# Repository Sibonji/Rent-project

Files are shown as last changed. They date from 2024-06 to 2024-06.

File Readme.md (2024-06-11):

# Проект: Вендинговый шкаф для аренды приборов (Phystech Rent)

## Команда:
Мухина Анфиса Дмитриевна: Дизайн модели большого шкафа; Создание 3д модели прототипа шкафа; Сборка прототипа; Построение схемы и тестирование замка
Сигбатулин Булат: Разработка веб интерфейса; Создание 3д модели прототипа шкафа; Сборка прототипа; Настройка взаимодействия сервера с NSP32.
Мотриченко Арсений: Создание 3д модели прототипа шкафа; Сборка прототипа; Дизайн веб интерфейса; Закупка комплектующих
Нвер Авагимян: Создание 3д модели прототипа шкафа; Сборка прототипа; Закупка комплектующих

## Описание продукта:
Необходимые предметы для быта занимают слишком много места, невзвешенные покупки, которые пылятся на полках, вещи, которые стоят стоят слишком дорого. Все эти проблемы может решить наш проект — вендинговый шкаф с почасовой арендой необходимой техники от пылесоса до плей стейшн.

Наш проект состоит из: шкафа, в котором будут храниться вещи для аренды, и сайта, через который можно бронировать определённый слот и завершать бронь, после использования.

## Цель работы
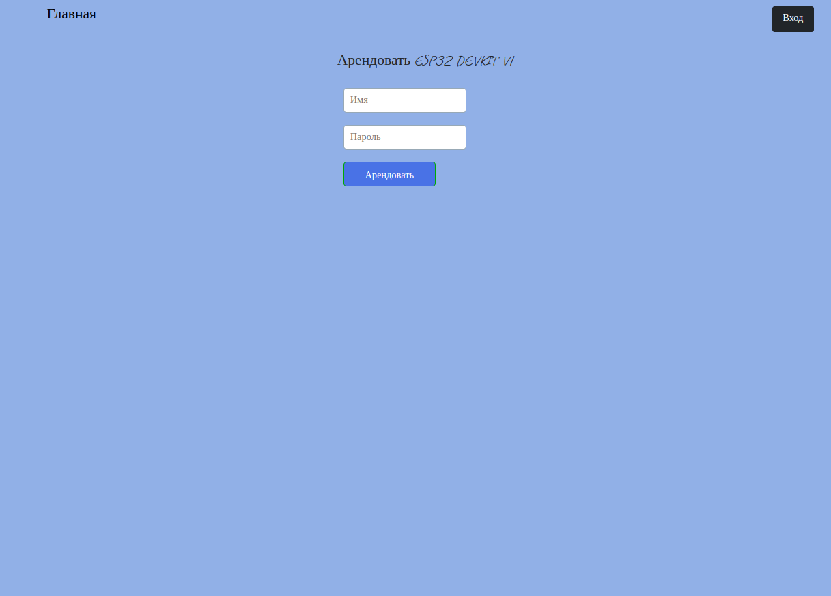
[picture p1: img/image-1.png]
Разработать прототип устройства и сервиса для удобной аренды различных вещей: бытовой техники, электронных комплектующих, инструментов и т.д. При некоммерческом использовании данное устройство может облегчить заимствование различных электронных устройств в Радиотехнической комнате (находится в 1 общежитии), Физтех Фабрике и на других площадках МФТИ. С помощью него можно будет избавиться от прослойки в виде ответственного за выдачу человека, иметь возможность "арендовать" (бесплатно) нужную вещь в любой время, а ответственному - просто и быстро отслеживать кто и когда взял в использование определенный предмет.

## Задачи

В ходе работы нужно будет решить несколько основных задач:
 - Посмотреть на существующие решения, и определить размеры и используемые материалы и комплектующие для нашего прототипа
 - Смоделировать прототип в специализированной программе (SolidWorks)
 - Собрать прототип
 - Релизовать программную модель прототипа
 - Релизовать сервис, через который будет осуществляться "аренда" в прототипе

## Анализ существующих аналогов

### Tulu

Это зарубежная компания, её нет на Российском рынке.

О постмате. В основном корпус выполнен из дерева, но имеются железные вставки. Такой выбор материала обеспечивает красивый вид, однако фанера, является более крепким материалом. Двери выполнены из стекла, это не самый надёжный вариант, но зато клиент может чётко видеть вещи, доступные к аренде, и их состояние. Замок на постматах Tulu не оснащён толкателем, он помогает клиенту понять, какой именно отсек активировался и облегчает открытие дверей, если в них нет ручек, но у шкафов Tulu дверцы прозрачные и в них добавлены ручки, что решает проблему.

Больгим приемуществом является доступность предметов для аренды, клиент не должен ждать достаку, и может сразу забрать продукт. В приложении есть временная гибкость, для вещей предусмотрена почасовая оплата. В отзывах люди жалуются на плохую работу приложения, например, польщователь переустанавливал его 3 раза прежде чем приложение заработало. Так же клиенты отмечают трудности с завершением аренды: приложение зависает и не даёт завершить аренду, в то время как деньги за арендованную вещь продолжают начисляться. Помимо всего прочего пользователи отмечают плохую работу поддержки, которая долго отвечает на сообщения, из-за этого у людей не получается вовремя решить проблему и они теряют деньги и время. 

### Арентер

Корпус постмата выполнен из железа, что даёт повышенную устойчивость к огню и воде. Часть дверей выполнены из стекла, часть полностью из железа не позволяя клиентам видеть, что находится внутри. На дверцах отсутствуют ручки, однако в ячейках стоят удобные замки с толкателем, что позволяет удобно открывать и закрывать дверь.

Арентер, как сервис по аренде, давно существует на Российском рынке, но аренду в формате постмата они ввели меньше месяца назад. По большей части эта компания ориентируется на то, что клиент сначала заказывает товар со склада, ждёт доставку и уже потом забирает предмет, это уменьшает доступность, поскольку клиент получает товар не сразу. Однако их приложение и предметы для аренды можно рассмотреть. У данного сервиса сложности с автоматизацией: непонятные цены, пользователи отмечают, что информация о ценах в приложении отличается от реальной, нет точной информации о том, что доступно в аренду, а что нет, любые вопросы уточняются через оператора, который зачастую отсутствует. 

### Наш вариант

Исследовав аналоги, мы поняли, что большое внимание стоит уделить приложению для аренды, нужно сделать его максимально прозрачным и минимизировать проблемы, о которых говорилось в отзывах у других компаний. Также мы решили реализовывать приложение в виде веб-интерфейса, так как это минимизирует проблемы, которые могут возникать из-за плохой поддержки приложения на разных устройствах. Рассмотрев различные реализации дверей постматов мы выбрали вариант со стеклом, это повышает заинтересованность пользователей и показывает, что вещи, хранящиеся в шкафу в надлежащем качестве. Возможно это не самый надёжный вариант, но в общежитии, где планируется применять наш шкаф, много камер, что повышает безопасность. Для уверенности можно привести в пример работу сервиса Self, который продаёт еду. Их товар лежит на полках, никак не закрытый, безопасность гарантируют качественные камеры, установленные на полках с товаром. Каркас нашего прототипа было решено сделать из фанеры, это надёжный и доступный материал. Для наилучшего скрепления составных частей шкафа мы сделали шиповое соединение у деталей. Двери мы решили делать без ручек в рамках экономии, удобное открытие гарантирует замок, который толкает дверь, чтобы она открылась широко. В качестве примера, на который мы впоследующем будем опираться, был нарисован примерный дизайн готового устройства:

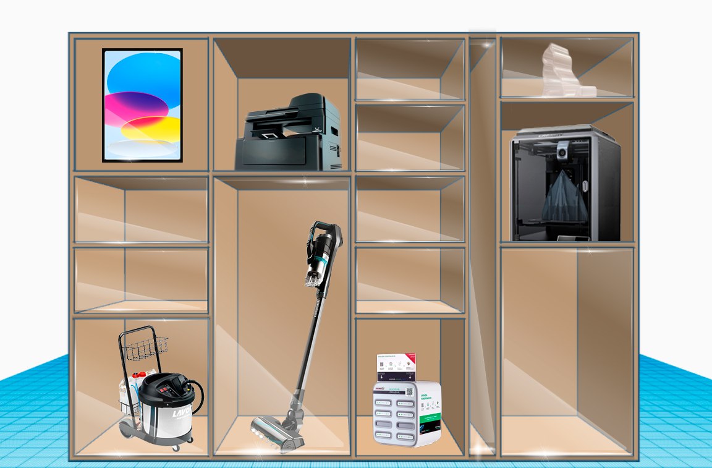
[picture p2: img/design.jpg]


## Ход работы

### Разработка корпуса

Модель разрабатывалась в приложении SolidWorks, в виде отдельных деталей, которые потом были объединены в виде сборки в том же приложении (детали и готовую сборку можно найти в папке box). Так как корпус будет вырезан из дерева было решено использовать для этого фрезерный станок, но перед этим, чтобы не тратить много дерева при неудаче, вырезать мини-модель с помощью лазерной резки:

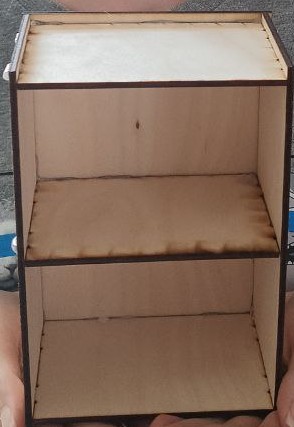
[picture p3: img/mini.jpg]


После того, как мы убедились что все корректно собралось на фрезерном станке, из фанеры толщиной 12мм, был вырезан корпус протипа:

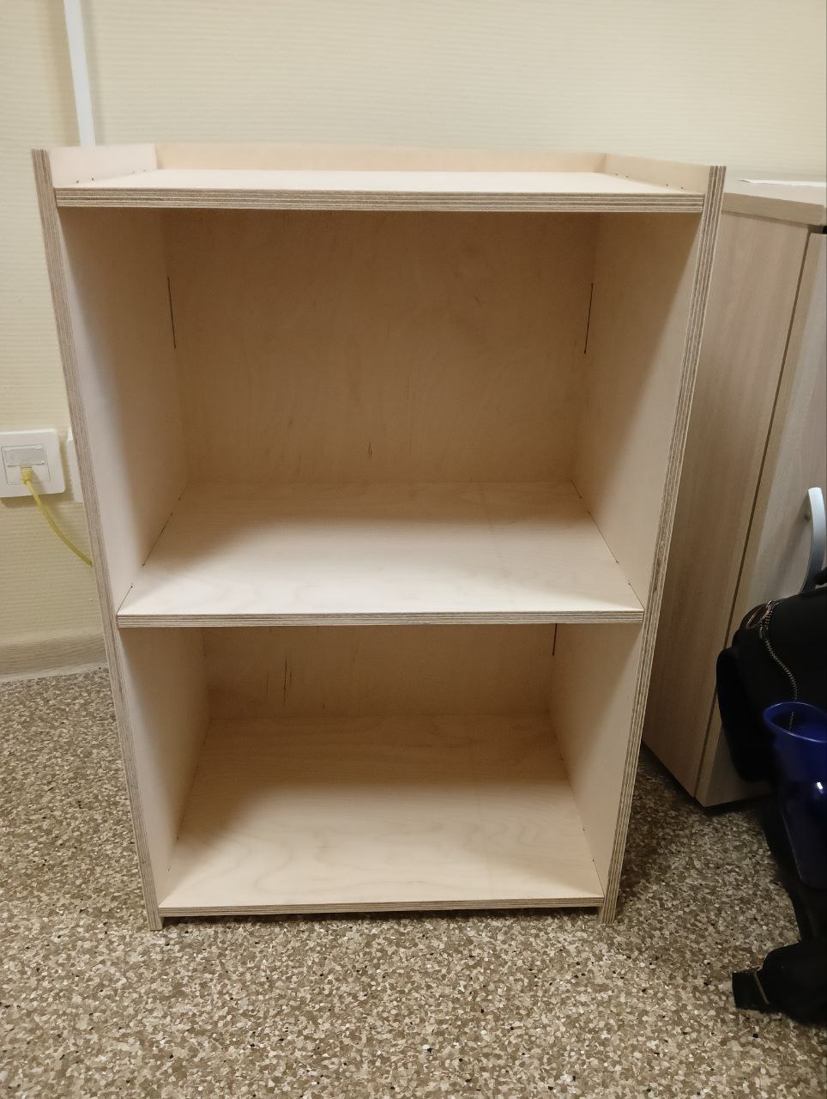
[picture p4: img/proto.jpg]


В завершении к корпусу были прикручены петли с стеклянными дверьми и электронные замки.

### Разработка электрической схемы

Теперь требуется определить электронную составляющую прототипа. Этим стали:

 - ESP32 - микроконтроллер, принимающий сигналы от веб сервера и управляющий замками.
 - XG07E Electronic Miniature Plastic Titanium Lock - замок используемый для открывания двери, с рабочим напряжением на входе.
 - Транзисторы TIP122 и резисторы на 1КОм для проектирования надежной электрической схемы открывания замка.

На картинке снизу представлена схема устройства, в качестве изображения замка используется схема элемента "логическое и":

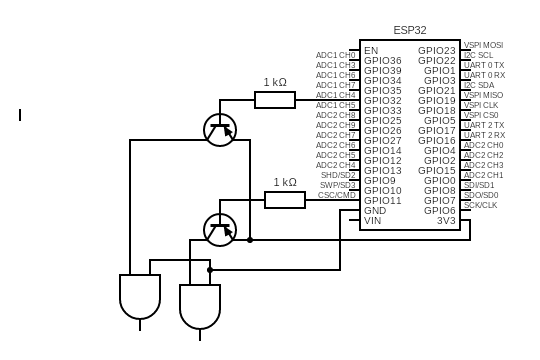
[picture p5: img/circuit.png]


Питание ESP32 в прототипе реализуется при помощи подключенного к порту micro-usb портативного зарядного устройства.

### Разработка сервера (веб-интерфейса) и клиента (код ESP32)

Сайт работает на основе библиотеки Flask (Python) с использованием баз данных под управлением MySQL. Данные хранятся в двух базах данных:
 - БД с пользователями (db/postamates.db)
 - БД с постаматами (user.db)

БД с пользователями хранит в себе одну таблицу - с информацией о пользователях:
 - Имя
 - Хэш пароля
 - Номер телефона

БД с постаматами хранит в себе 2 таблицы, таблицу с информацией о постаматах:
 - Id постамата
 - Ip адрес постамата (ESP32)
 - Расположение постамата

И таблицу с информацией о ячейках в каждом постамате:
 - Id постамата
 - Id ячейки (привязана к пину GPIO на ESP32, через который ячейка открывается)
 - Статус ячейки (есть ли там что-то или нет)
 - Id пользователя, который в последний раз оттуда что-то брал
 - Дата и время, когда оттуда что-то брали в последний раз
 - Информация о предмете, который там лежит

Код ESP32, хоть и называется клиентом, в свою очередь также является небольшим веб-сервером. Он представляет собой набор ссылок строящихся по шаблону - <esp_ip_addr>/<GPIO_PIN>/on. Здесь:
 - esp_ip_addr это ip адресс присваеваемый ESP
 - GPIO_PIN - номер пина GPIO, который управляет открытием и закрытием определенной ячейки.

При бронировании и возвращении предмета в ячейку, сайт (сервер) обращается по соответствующей ссылке ESP32 (клиента), а тот в свою очередь считывает это обращение и открывает ячейку. Открытие ячейки занимает определенное время из-за электрических характеристик замка. При входном напряжении 3 Вольта замку требуется чуть меньше 1 секунды на открытие, так как напряжение с выхода ESP32 подается сразу на два замка, это время было увеличено до 1,5 секунд, чтобы обеспечить стабильную работу устройства. Для бронирования необходимо перейти на сайт, выбрать постамат в нужной локации и устройство, которое вы хотите взять:

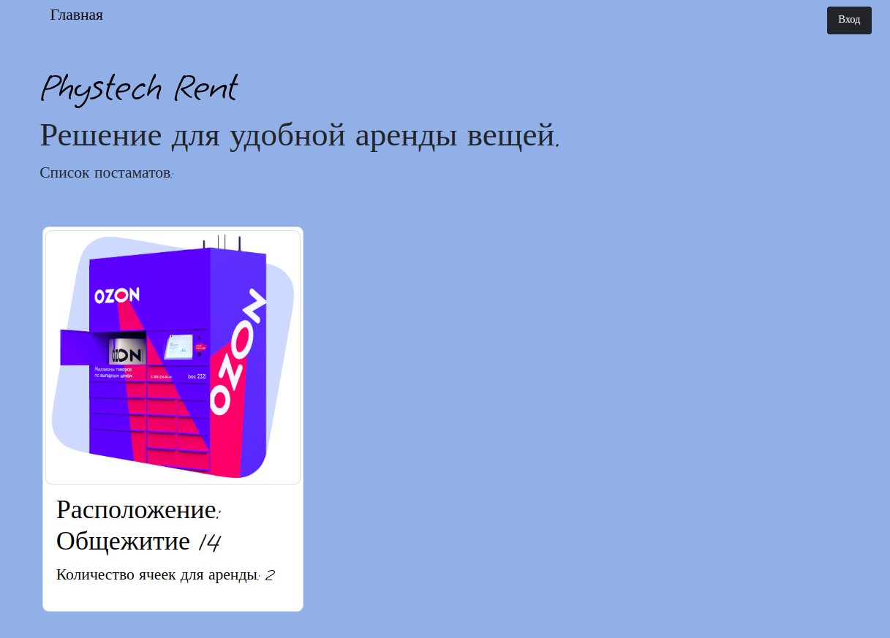
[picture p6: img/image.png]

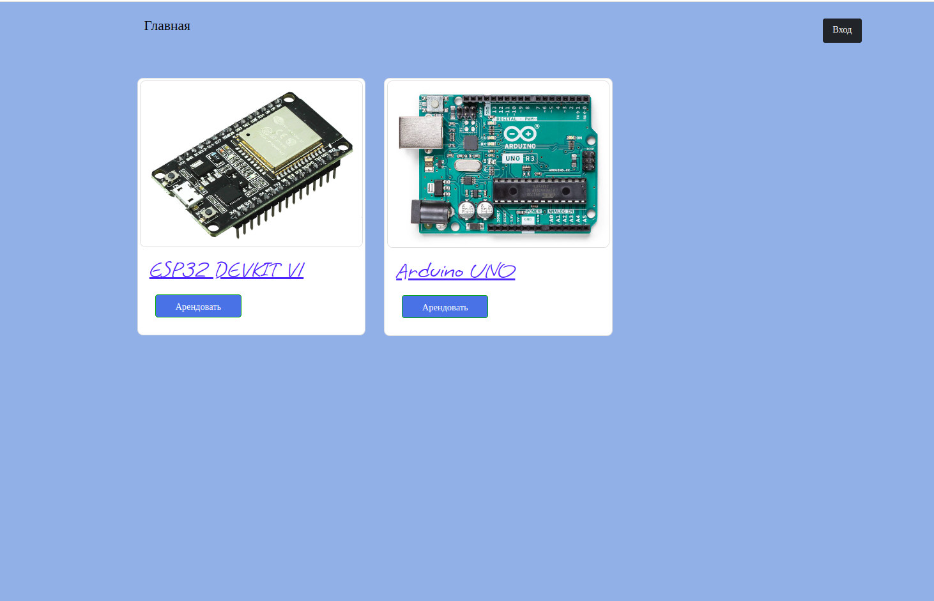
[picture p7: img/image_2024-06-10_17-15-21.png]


Для того, чтобы сайт определил кто вы и сохранил эту информацию нужно войти в свой аккаунт:



После того, как предмет арендован, на сайте будет невозможно его арендовать. Чтобы закончить аренду, нужно войти в свой аккаунт, нажав на кнопку вход в правом верхнем углу и кнопку завершить аренду:

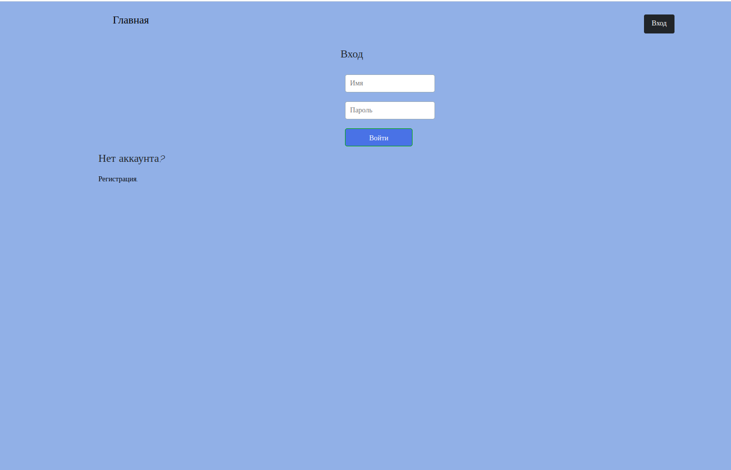
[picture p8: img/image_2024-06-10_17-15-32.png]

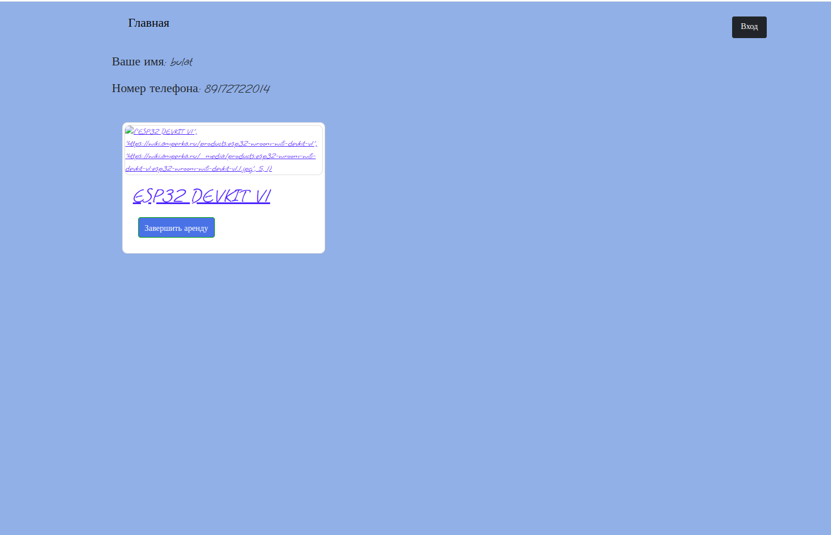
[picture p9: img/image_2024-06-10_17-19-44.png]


## Проблемы возникшие в ходе работы

Успешный продукт (и его отдельные компоненты), как это часто бывает, был получен не сразу. Во время работы нас преследовало множество проблем и недочетов. Первой проблемой, с которой мы столкнулись, был недочет в вырезанных из фанеры на фрезере деталях. Она заключалась в том, что мы хоть и заложили в модели запас в 0.5 мм в расстоянии пазов по длине, забыли сделать то же самое по ширине. Из-за данного недочета, для того чтобы модель собралась мы сняли небольшой слой дерева на каждом из проблемных участков при помощи наждачной бумаги.

Вторая проблема возникла при работе с замком и ESP32. Изначальная идея заключалась в том, чтобы подключать один из входов замка напрямую к управляющему пину, в надежде на то, что при уровне сигнала соответствующем логической единице замок будет открываться. Однако ничего не происходило, хотя если подключать замок к выходам GND и 3.3 Вольт, замок сразу же открывался. Последующее тестирование показало, что при подключении замка к выходу GPIO, на нем сразу происходит падение напряжение, что не наблюдается на выходе 3.3 Вольт. Поэтому было решено подавать напряжение на замок с выхода 3.3 Вольт, через транзистор, а транзистором уже управлять при помощи пина GPIO. Также, чтобы ток, подавающийся на базу транзистора соответствовал требованиям документации, между выходом GPIO и базой транзистора был добавлен резистор с сопротивлением в 1 Ком.

И последняя проблема возникла при подключении к пину 3.3 Вольта 2 и более замков (с транзисторами). В таких случаях напряжение стало падать, а замку требоваться больше времени для открытия. Поэтому решением стало увеличить время задержки сигнала на высоком уровне с 1 секунды до 1.5 секунд.

## Результаты

Был разработан полностью рабочий прототип устройства для аренды различного типа предметов. В дополнение был создан веб-интерфейс для удобной работы с данным устройством со стороны клиента.

Полученный прототип успешно показал себя на тестах (видео) и даже может быть использован при желании.

<video controls src="img/video_2024-06-10_18-04-13.mp4" title="Видео работы устройства"></video>

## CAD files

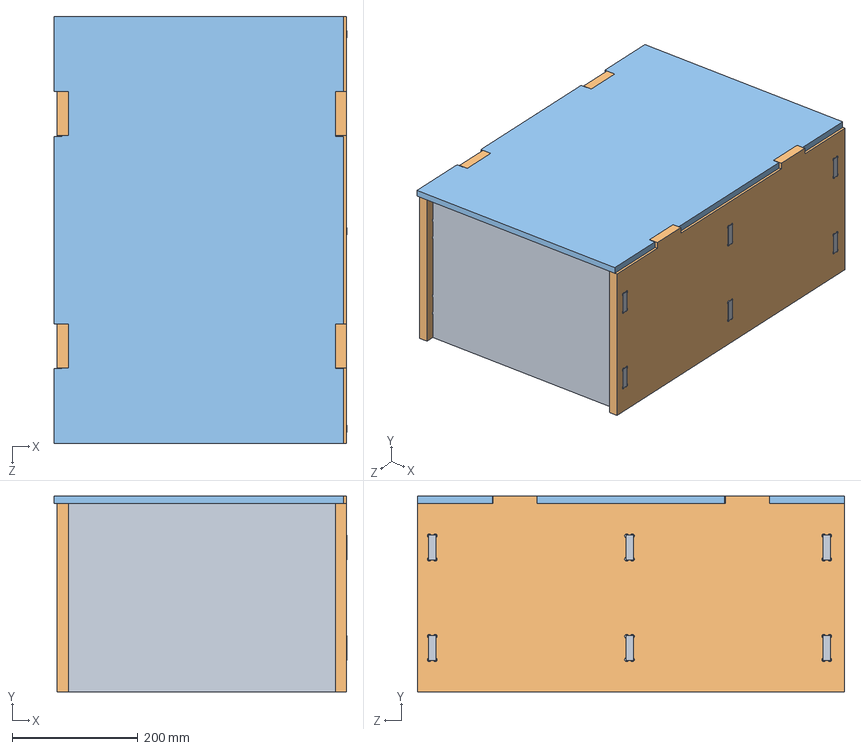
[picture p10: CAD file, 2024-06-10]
box/Assem1.SLDASM
466.5 x 312.0 x 680.5 mm
полка x 3
Боковая x 2
Деталь111

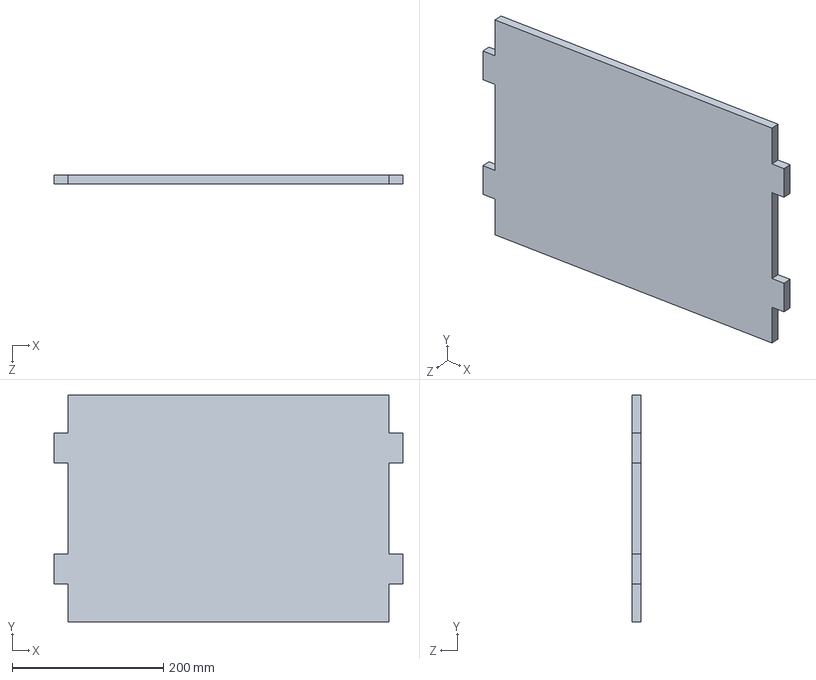
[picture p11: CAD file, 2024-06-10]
box/полка.SLDPRT
462.0 x 300.0 x 12.0 mm

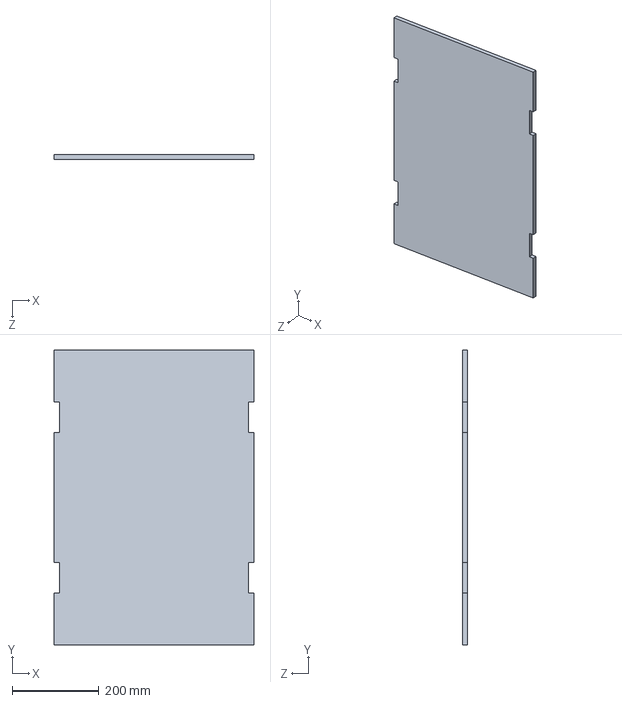
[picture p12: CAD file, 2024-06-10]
box/Деталь111.SLDPRT
461.0 x 680.0 x 12.0 mm

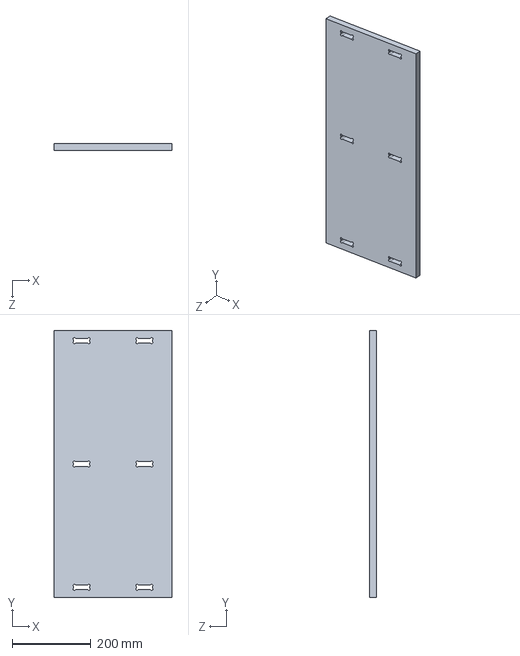
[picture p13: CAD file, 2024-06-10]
box/Боковая.SLDPRT
300.0 x 680.0 x 18.0 mm

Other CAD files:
box/Back.SLDPRT
box/Боковая.DXF
box/Деталь111.DXF
box/полка.DXF

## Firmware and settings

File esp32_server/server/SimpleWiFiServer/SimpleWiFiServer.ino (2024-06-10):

// Загружаем библиотеку Wi-Fi
#include <WiFi.h>

// Замените на свой идентификатор и пароль
const char* ssid = "TESTNET";
const char* password = "StudentPass50";

// Номер порта для сервера
WiFiServer server(80);

// HTTP-запрос
String header;

// текущее состояние кнопки
String output5State = "off";
String output27State = "off";
// Номера выводов
const int output5 = 5;
const int output27 = 27;

void setup() {
  Serial.begin(115200);
  // Настраиваем выводы платы
  pinMode(output5, OUTPUT);
  // Переводим выводы в LOW
  digitalWrite(output5, LOW);

  // Подключаемся к Wi-Fi
  Serial.print("Connecting to ");
  Serial.println(ssid);
  WiFi.begin(ssid, password);
  while (WiFi.status() != WL_CONNECTED) {
    delay(500);
    Serial.print(".");
  }
  // Выводим локальный IP-адрес и запускаем сервер
  Serial.println("");
  Serial.println("WiFi connected.");
  Serial.println("IP address: ");
  Serial.println(WiFi.localIP());
  server.begin();
}

void loop() {
  WiFiClient client = server.available(); // прослушка входящих клиентов
  if (client) { // Если подключается новый клиент,
    Serial.println("New Client."); // выводим сообщение
    String currentLine = "";
    while (client.connected()) { // цикл, пока есть соединение клиента
      if (client.available()) { // если от клиента поступают данные,
        char c = client.read(); // читаем байт, затем
        Serial.write(c); // выводим на экран
        header += c;
        if (c == '\n') { // если байт является переводом строки
          // если пустая строка, мы получили два символа перевода строки
          // значит это конец HTTP-запроса, формируем ответ сервера:
          if (currentLine.length() == 0) {
            // HTTP заголовки начинаются с кода ответа (напр., HTTP / 1.1 200 OK)
            // и content-type, затем пустая строка:
            client.println("HTTP/1.1 200 OK");
            client.println("Content-type:text/html");
            client.println("Connection: close");
            client.println();

            // Включаем или выключаем светодиоды
            if (header.indexOf("GET /5/on") >= 0) {
              Serial.println("GPIO 5 on");
              output5State = "on"; //добавить проверку на то, что замок еще не открылся в цикле
              digitalWrite(output5, HIGH);
              delay(1400);
              digitalWrite(output5, LOW);
            } else if (header.indexOf("GET /5/off") >= 0) {
              Serial.println("GPIO 5 off");
              output5State = "off"; //дверь закрыта
              
            } else if (header.indexOf("GET /27/on") >= 0) {
              Serial.println("GPIO 27 on");
              output27State = "on"; //добавить проверку на то, что замок еще не открылся в цикле
              digitalWrite(output27, HIGH);
            } else if (header.indexOf("GET /27/off") >= 0) {
              Serial.println("GPIO 27 off");
              output27State = "off"; //дверь закрыта
              digitalWrite(output27, LOW);
            }
            // Формируем веб-страницу на сервере
            client.println("<!DOCTYPE html><html>");
            client.println("<head><meta name=\"viewport\" content=\"width=device-width, initial-scale=1\">");
            client.println("<link rel=\"icon\" href=\"data:,\">");
            // CSS для кнопок
            // можете менять под свои нужды
            client.println("<style>html { font-family: Helvetica; display: inline-block; margin: 0px auto; text-align: center;}");
            client.println(".button { background-color: #4CAF50; border:  none; color: white; padding: 16px 40px;");
            client.println("text-decoration: none; font-size: 30px; margin: 2px; cursor: pointer;}");
            client.println(".button2 {background-color:#555555;}</style></head>");
            client.println("<body><h1>ESP32 Web Server</h1>");
            // Выводим текущее состояние кнопок
            client.println("<p>GPIO 5 - State " + output5State + "</p>");
            // Если output5State сейчас off, то выводим надпись ON
            if (output5State == "off") {
              client.println("<p><a href=\"/5/on\"><button class=\"button\">ON</button></a></p>");
            } else {
              client.println("<p><a href=\"/5/off\"><button class=\"button button2\">OFF</button></a></p>");
            }
            // Аналогично для второй кнопки
            client.println("<p>GPIO 27 - State " + output27State + "</p>");
            if (output27State == "off") {
              client.println("<p><a href=\"/27/on\"><button class=\"button\">ON</button></a></p>");
            } else {
              client.println("<p><a href=\"/27/off\"><button class=\"button button2\">OFF</button></a></p>");
            }
            client.println("</body></html>");
            // HTTP-ответ завершается пустой строкой
            client.println();
            break;
          } else { // если получили новую строку, очищаем currentLine
            currentLine = "";
          }
        } else if (c != '\r') { // Если получили что-то ещё кроме возврата строки,
          currentLine += c; // добавляем в конец currentLine
        }
      }
    }
    // Очистим переменную
    header = "";
    // Закрываем соединение
    client.stop();
    Serial.println("Client disconnected.");
    Serial.println("");
  }
  // else {
  //   if (output5State == "on") { //добавить проверку на то, что дверь закрылась
  //     Serial.println("Door unlocked");
  //     client.println("HTTP/1.1 200 OK");
  //     client.println("Content-type:text/html");
  //     client.println("Connection: close");
  //     client.println();

  //     // Формируем веб-страницу на сервере
  //     client.println("<!DOCTYPE html><html>");
  //     client.println("<head><meta name=\"viewport\" content=\"width=device-width, initial-scale=1\">");
  //     client.println("<link rel=\"icon\" href=\"data:,\">");
  //     // CSS для кнопок
  //     // можете менять под свои нужды
  //     client.println("<style>html { font-family: Helvetica; display: inline-block; margin: 0px auto; text-align: center;}");
  //     client.println(".button { background-color: #4CAF50; border:  none; color: white; padding: 16px 40px;");
  //     client.println("text-decoration: none; font-size: 30px; margin: 2px; cursor: pointer;}");
  //     client.println(".button2 {background-color:#555555;}</style></head>");
  //     client.println("<body><h1>ESP32 Web Server</h1>");
  //     // Выводим текущее состояние кнопок
  //     client.println("<p>GPIO 5 - State " + output5State + "</p>");
  //     // Если output5State сейчас off, то выводим надпись ON
  //     client.println("<p><a href=\"/5/off\"><button class=\"button button2\">OFF</button></a></p>");
  //     output5State = "off";
      
  //     // Аналогично для второй кнопки
  //     client.println("<p>GPIO 27 - State " + output27State + "</p>");
  //     if (output27State == "off") {
  //       client.println("<p><a href=\"/27/on\"><button class=\"button\">ON</button></a></p>");
  //     } else {
  //       client.println("<p><a href=\"/27/off\"><button class=\"button button2\">OFF</button></a></p>");
  //     }
  //     client.println("</body></html>");
  //     // HTTP-ответ завершается пустой строкой
  //     client.println();
  //   }
  //   else if (output27State == "on") { //добавить проверку на то, что дверь закрылась
  //     Serial.println("Door unlocked");
  //     client.println("HTTP/1.1 200 OK");
  //     client.println("Content-type:text/html");
  //     client.println("Connection: close");
  //     client.println();

  //     // Формируем веб-страницу на сервере
  //     client.println("<!DOCTYPE html><html>");
  //     client.println("<head><meta name=\"viewport\" content=\"width=device-width, initial-scale=1\">");
  //     client.println("<link rel=\"icon\" href=\"data:,\">");
  //     // CSS для кнопок
  //     // можете менять под свои нужды
  //     client.println("<style>html { font-family: Helvetica; display: inline-block; margin: 0px auto; text-align: center;}");
  //     client.println(".button { background-color: #4CAF50; border:  none; color: white; padding: 16px 40px;");
  //     client.println("text-decoration: none; font-size: 30px; margin: 2px; cursor: pointer;}");
  //     client.println(".button2 {background-color:#555555;}</style></head>");
  //     client.println("<body><h1>ESP32 Web Server</h1>");
  //     // Выводим текущее состояние кнопок
  //     client.println("<p>GPIO 5 - State " + output5State + "</p>");
  //     // Если output5State сейчас off, то выводим надпись ON
  //     if (output5State == "off") {
  //       client.println("<p><a href=\"/5/on\"><button class=\"button\">ON</button></a></p>");
  //     } else {
  //       client.println("<p><a href=\"/5/off\"><button class=\"button button2\">OFF</button></a></p>");
  //     }
  //     // Аналогично для второй кнопки
  //     client.println("<p>GPIO 27 - State " + output27State + "</p>");
  //     client.println("<p><a href=\"/27/off\"><button class=\"button button2\">OFF</button></a></p>");
  //     output27State = "off";
  //     client.println("</body></html>");
  //     // HTTP-ответ завершается пустой строкой
  //     client.println();
  //   }
  // }
}

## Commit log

2024-06-10 Added esp32 code
2024-06-10 Added model files
    [Assem1.SLDASM, Back.SLDPRT, Боковая.DXF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]
2024-06-10 Added description, fixed minor errors, completed esp32 client
    [SimpleWiFiServer.ino]
